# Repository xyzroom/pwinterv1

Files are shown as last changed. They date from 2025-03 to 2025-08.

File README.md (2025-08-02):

# P-Winter V1 (archive)

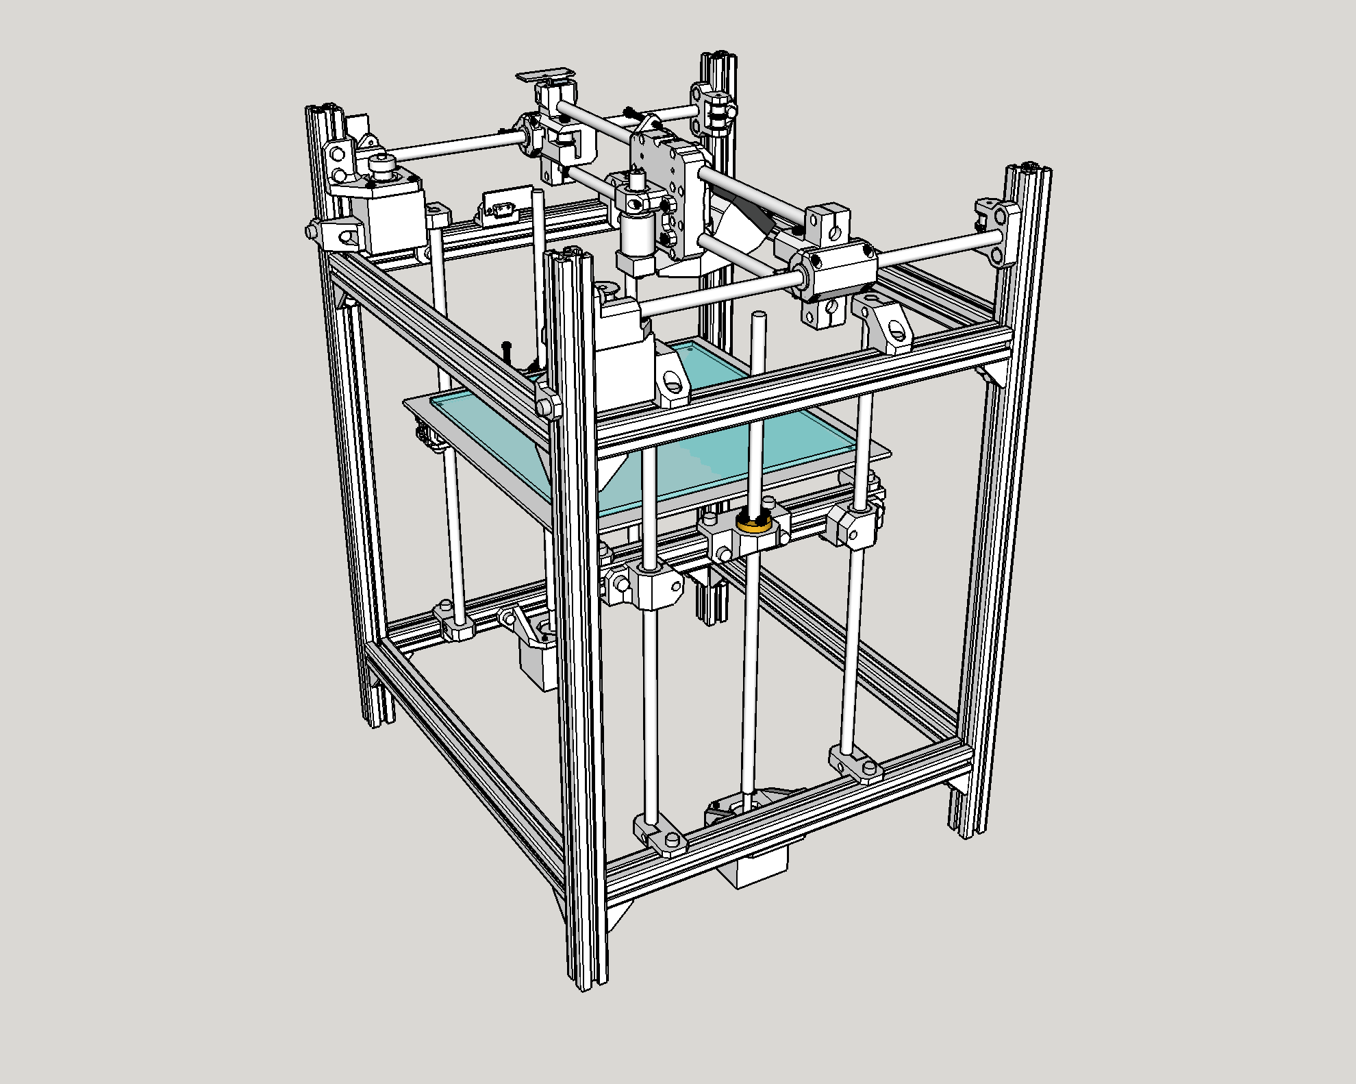
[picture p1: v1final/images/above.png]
front image


## Welcome
- P-Winter is a CoreXY 3D printer. It aims for an accessible BOM and assembly, with drop-in nuts and a fully-bracketed frame.
- There are major flaws with this design. It was made predominantly when I was 14 with zero experience.
- I am working on P-Winter V2, which will reuse most of the components iron out some silly design flaws and misunderstandings from V1. Well, I had basically completed the V2 concept in SketchUp, but when I went to model it properly in Fusion 360, the files had disappeared! >:(
- V1 cost estimate: approx 50 GBP for non-printed parts in the final printer, not including prototyping waste.

# V2 Changes
## Overview
There were a few fatal flaws and inconveniences with V1. V2 strives to fix most of these. V2 primarily aims for a more sensible belt path, a more sensible Z axis, a filtered enclosure, a (larger) more sensible build volume.

## Dimensions and V2 Enclosure
- V1 Frame (2020 T-slot extrusions): 380mm x 340mm x 500mm
- V1 Build volume: approx 210mm x 199mm x 270mm
- V2 will use the same frame with added extrusions for the enclosure and other attachments (e.g. filters).
##
- The V1 frame was not enclosable due to part of the XY spilling out to the sides and to the top.
- V2 changes this, compacting the design while offering a larger build volume. The current build footprint in CAD is at least a comfortable 220mm x 220mm.
- The Z axis is being shortened to enable the toolhead's Bowden tube and wiring to be enclosed comfortably.
- Previously, the electronics for V1 where pulled outside an external enclosure to keep them cool. For V2, the electronics will be hidden at the bottom of the printer, separated from the heated chamber via an air gap.
- Some enclosure circulation/filtration shenanigans.

## CoreXY
- V1 uses 8mm linear rods: 2x 300mm for Y and 2x 350mm for X.
- These are retained for V2. V2 will use LM8LUUs for Y and LM8UUs/LM8LUUs for X.
##
- V1 used 16T GT2 pulleys and idlers and 6mm steel-core GT2 belts, with 38mm NEMA 17 stepper motors.
- The knockoff pulleys and idlers had questionable bearing quality/centred-ness/profile accuracy. Additionally, I had spaced them incorrectly in the previous belt path. The idlers also did not operate smoothly on the threaded bolts I was using to hold them.
- The steel-core belts had questionable thickness and were incompatible with the small bend radius of the 16T pulleys and idlers.
- V2 will use proper belts and use stacked F695 flanged bearings as idlers. These have larger bearings suited for motion, are more likely to be round and centred, and also have more predictable dimensions than cheap toothed idlers. V2 will use dowel pins to hold these idlers properly.
##
- V1 used a Hypercube-based belt path where the AB motors occupied space at the front of the Y axis. The motors were an eyesore and limited the travel in Y.
- The belt path has been completely redrawn for V2. It is now correctly aligned and parallel, and I have brought it as close to the enclosed extremities as possible, increasing travel significantly in both X and Y. The AB motors have been moved to the back of the frame.
- The AB motors no longer need to be aligned with the belt path. The diameter of the pulleys no longer matter either. Either 16T or 20T can be used with minimal modification.
##
- Some magic with the belt path leaves 307mm of available rod length in the X axis. This allows for an 85mm-wide X carriage to travel 220mm comfortably in the X direction.
- The motors being in the back of the frame increases the available rod length to 267mm (up to 282mm). A 45mm-wide Y carriage can confortably travel 220mm in the Y direction.
- These limits can be pushed, but I am sticking to (220mm)^2 for now. The bed is (250mm)^2 so I can modify printer dimensions as desired after I get it working.
##
- In V1, the motor mounts began to deform due to belt tension and motor weight acting together. The V2 motor positioning allows for a stronger, thicker mount with better-placed bolting holes. The belt tension now acts against the weight of the motor.

## Z axis
- V1 used a dual-Z setup with two 8mm x 350mm linear rods and a 350mm leadscrew on each side of the frame. (The 350mm leadscrew is too long for 350mm linear rods when using regular leadscrew nuts but this is not a major issue). This offered approximately 270mm in vertical travel
- V2 will use a similar setup with 4 rods and 2 (maybe 3) leadscrews, but shorten the Z axis to enclose the printer better.
##
- The original V1 -> V2 plan was to implement automatic bed levelling with three independent leadscrews. I decided against this because an effective triple Z requires an additional axis, two additional steppers and two additional drivers. There is a risk of overconstraint and having 3 leadscrews may introduce other artefact problems. Overall these are resources I would prefer to allocate to my 300mm printer project.
- I might still add a ABL sensor to V2.
- A 220mm printer really should just be properly trammed...
##
- The V1 setup used separate Z carriages on each side of the printer, connected only via the heated bed and bed levelling springs. The carriages were atrocious to tram relative to each other and to the frame.
- V2 will use a rectangular frame made from 4 extrusions, with the bed bolted directly to the T-slot channels using silicon spacers. This will be far stiffer and easier to level.

## Toolhead
- V1 used a V6 Volcano clone in a Bowden setup. V2 will keep this or use a HGX-LITE clone in direct drive.
- V1 did not end up with any part cooling. My newbie duct design had nil airflow and collided with the belts in the back, so I got rid of it and left it to V2.
- V2 will use dual 5015s for part cooling.

## Electronics
- The original setup was a classic 12V Mega/RAMPS/A4988 setup running Marlin 2.0. This was undeniably the cheapest possible setup and what I'm used to.
- Marlin took forever to compile. 3-axis hardware is not hard to build, but I'd like to get more involved with the software side of 3D printers. The new setup will run on Klipper and have an ADXL which will be fun.
- I will be switching from 12V to 12V + 24V electronics. The heated bed could barely reach 75 deg C, so I will be supplying 24V to at least the heated bed, and potentially other components if I ever need to push performance.
- Silent stepper drivers.
- Known thermistors rather than mystery 100k.

## V1 Performance and Other V2 Improvements
- Prints suffered from a wobble/layer shifting in the Y direction, on average in the correct position. I suspect this was due to play in the X axis rods and hot end nozzle, misalignment in the belt path and improperly-tuned stepper drivers. In V2, rods and bearings will be clamped down on rather than clipped or press-fitted into place.
- V1 homing used Makerbot-style endstops that are triggered by adjustable bolts on the moving carriage. This precision adjustment was good for the Z axis but unnecessary for the X and Y axes. Switching to simpler triggers.
- In general V2 is a design made by a more experienced me. The parts are more functional and the CAD is more detailed, avoiding issues in V1 where the lack of detail meant that bolts were inaccessible or that things would collide with the belt path. New models check for interference, etc and are much more mature.

## V2 Predicted Issues/Advice To Self
- Centre of mass imbalance on the X rods.
- Check the continuity of endstop switches and the resistance of heaters/thermistors with a multimeter. It took forever to figure out why the linear voltage regulator on my Mega kept frying. There was a solder bridge short circuit on one of my endstops!!!
- Tune steppers properly.

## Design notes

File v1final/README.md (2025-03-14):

# v1 final (dec2024)
## Comments
- 3.2mm holes for M3
- 5mm holes for M5 bolts - In V2, these will be 5.2mm
- 2.9mm holes for screwing M3 into plastic - In V2, this will be replaced by circles with tabs
- Dowel pins for idlers in V2
- In V2, built-in bridge supports for overhanging holes will be replaced.
- In V2, eliminated circular overhangs
- In V2, consider notches in tight fit holes to prevent seam line interferance

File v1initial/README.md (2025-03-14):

# v2 initial
## Comments
These are initial files for the machine, barely usuable.
- The old x carriage had issues gripping onto the linear bearings and flexed under belt tension. The new x carriage clamps on the bearings and is not missing so much material.
- The new hot end mount grips onto the E3D V6 cooling fins using a zip tie for added stability.
- The new y carriages clamp onto the x linear rods, adding stability.
- The y rod/roller mounts are now more reliable to align with the frame.
- Some distances have been changed, with some yet to change

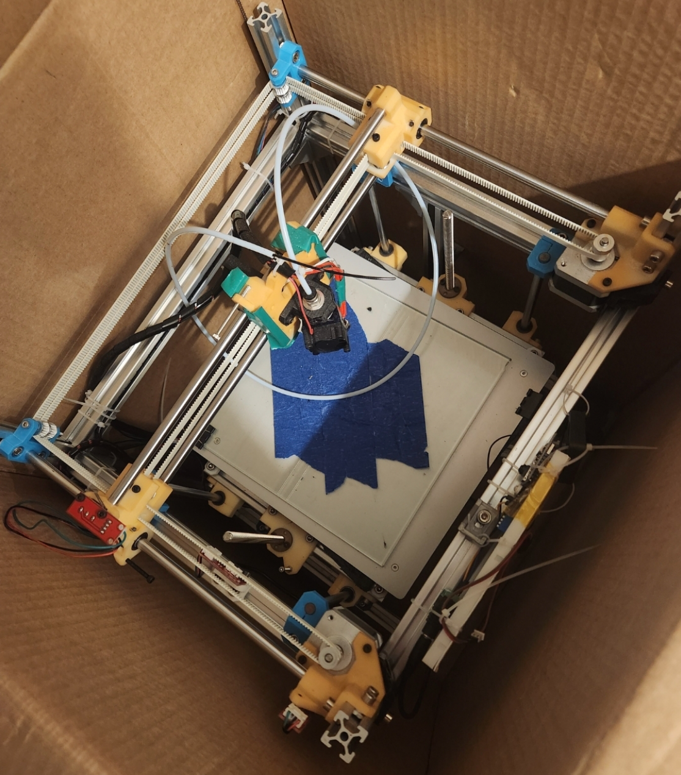
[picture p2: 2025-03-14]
v1final/images/wide.png

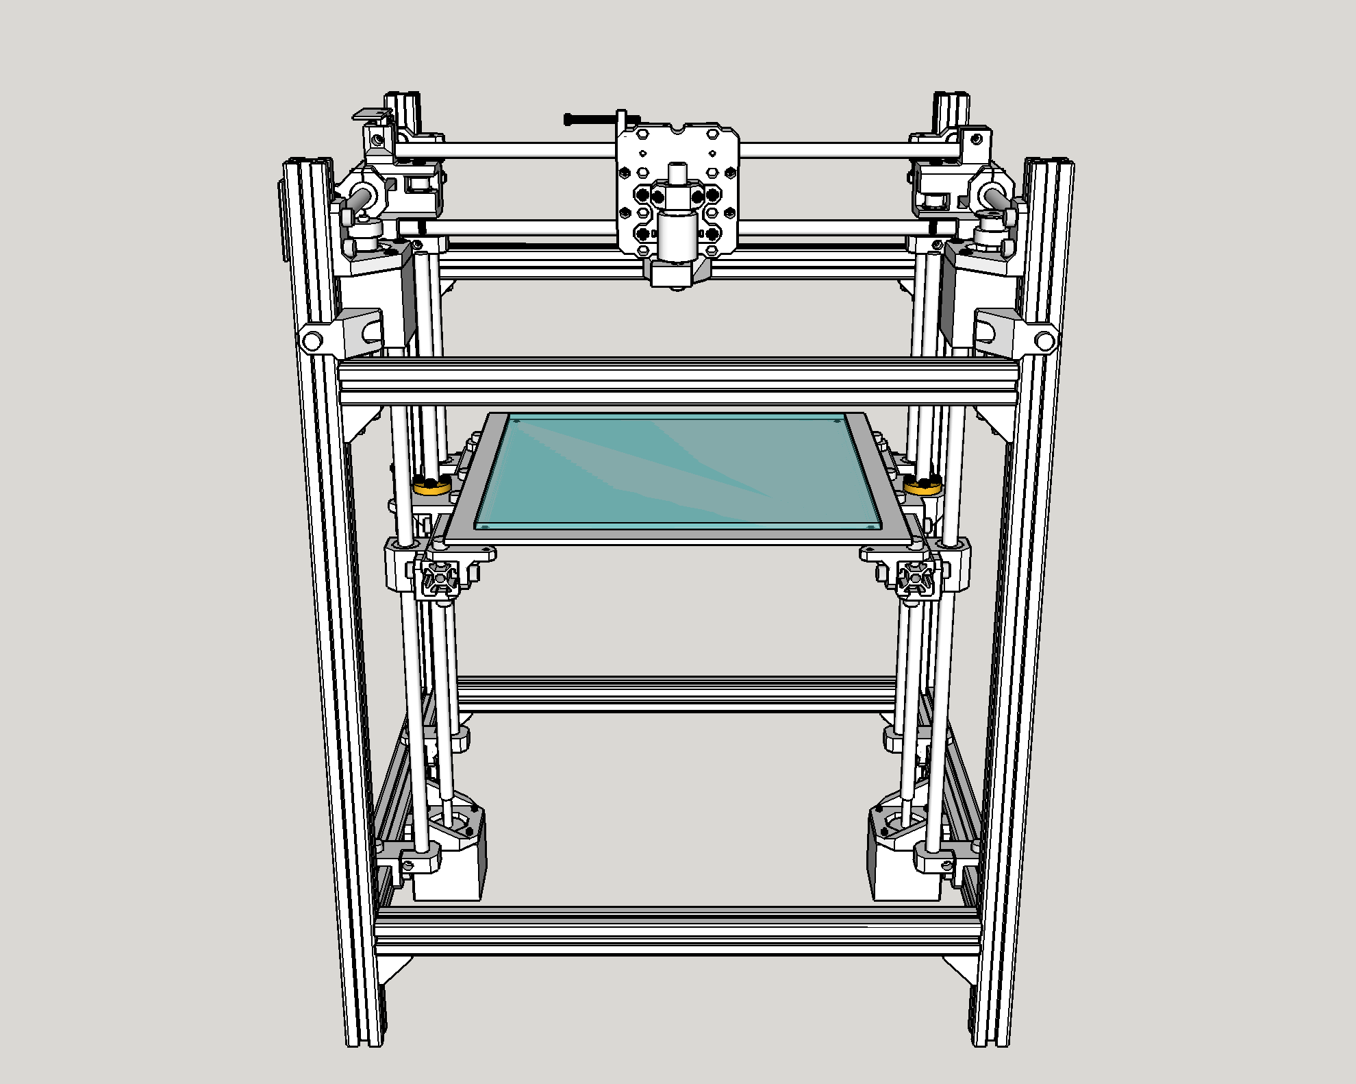
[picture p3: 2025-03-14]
v1final/images/front.png

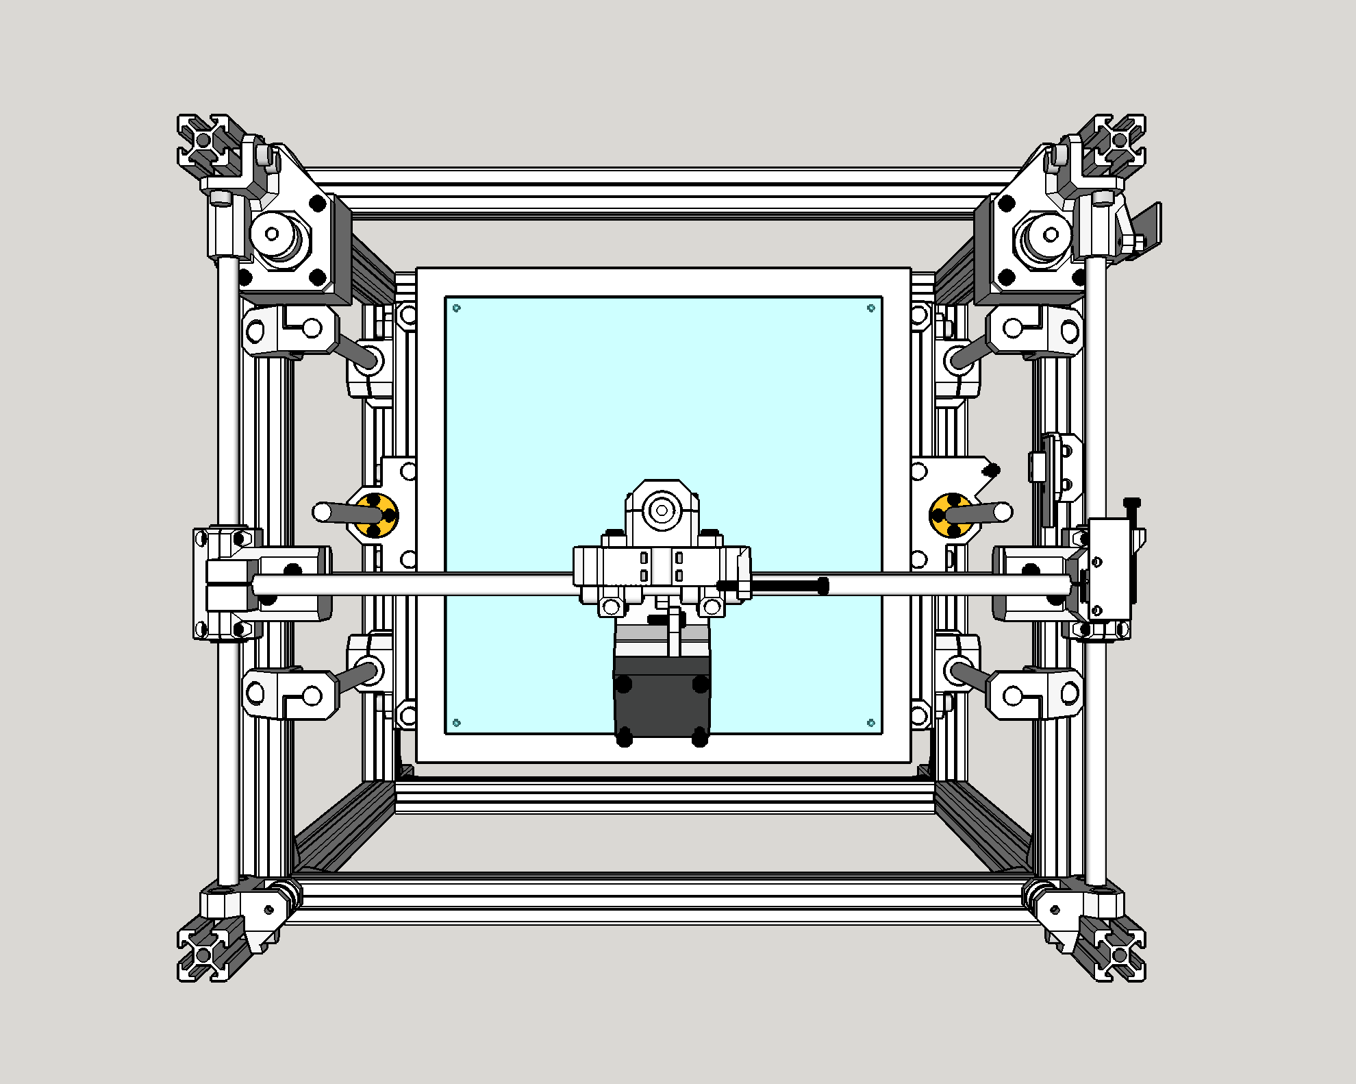
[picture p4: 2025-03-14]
v1final/images/top.png

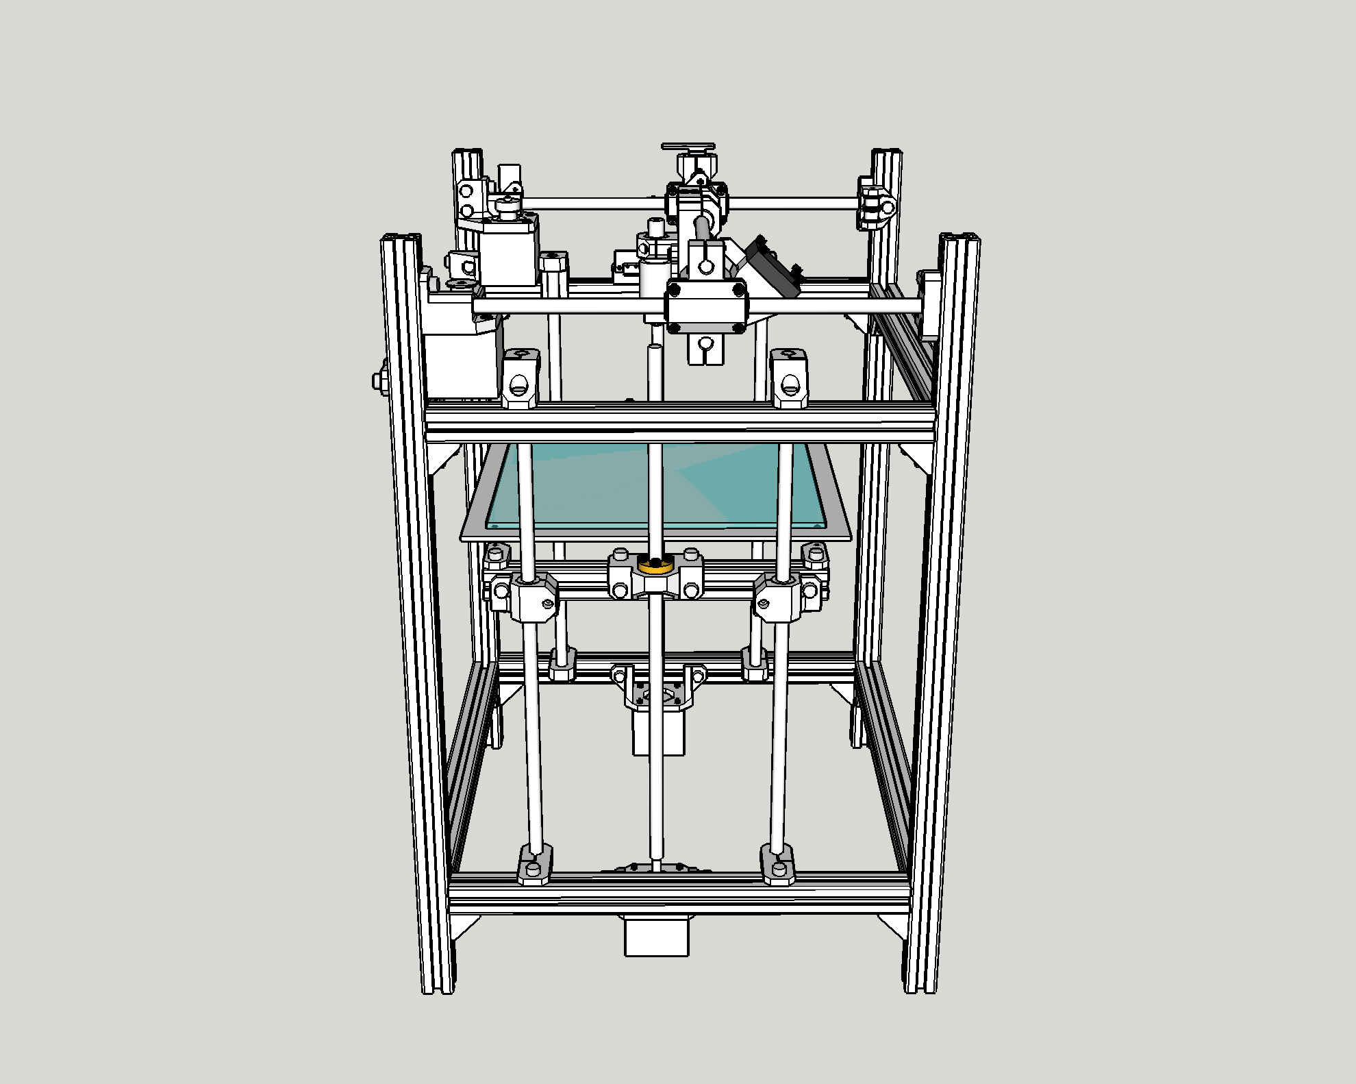
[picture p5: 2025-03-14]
v1final/images/side.png

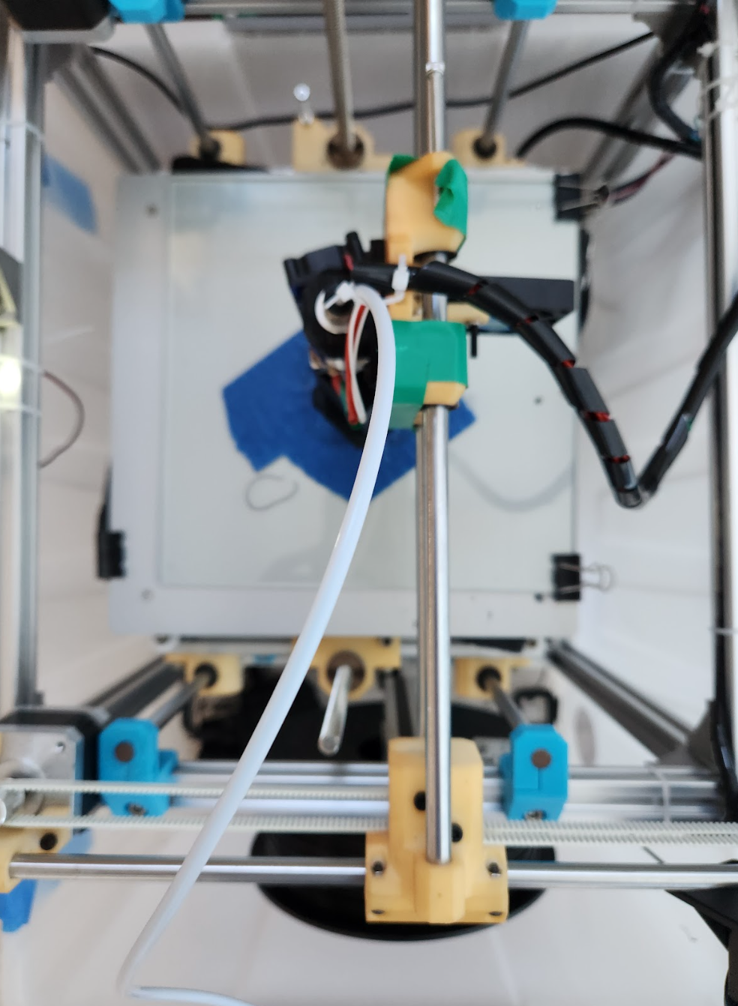
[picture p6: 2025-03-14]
v1final/images/toppicture.png

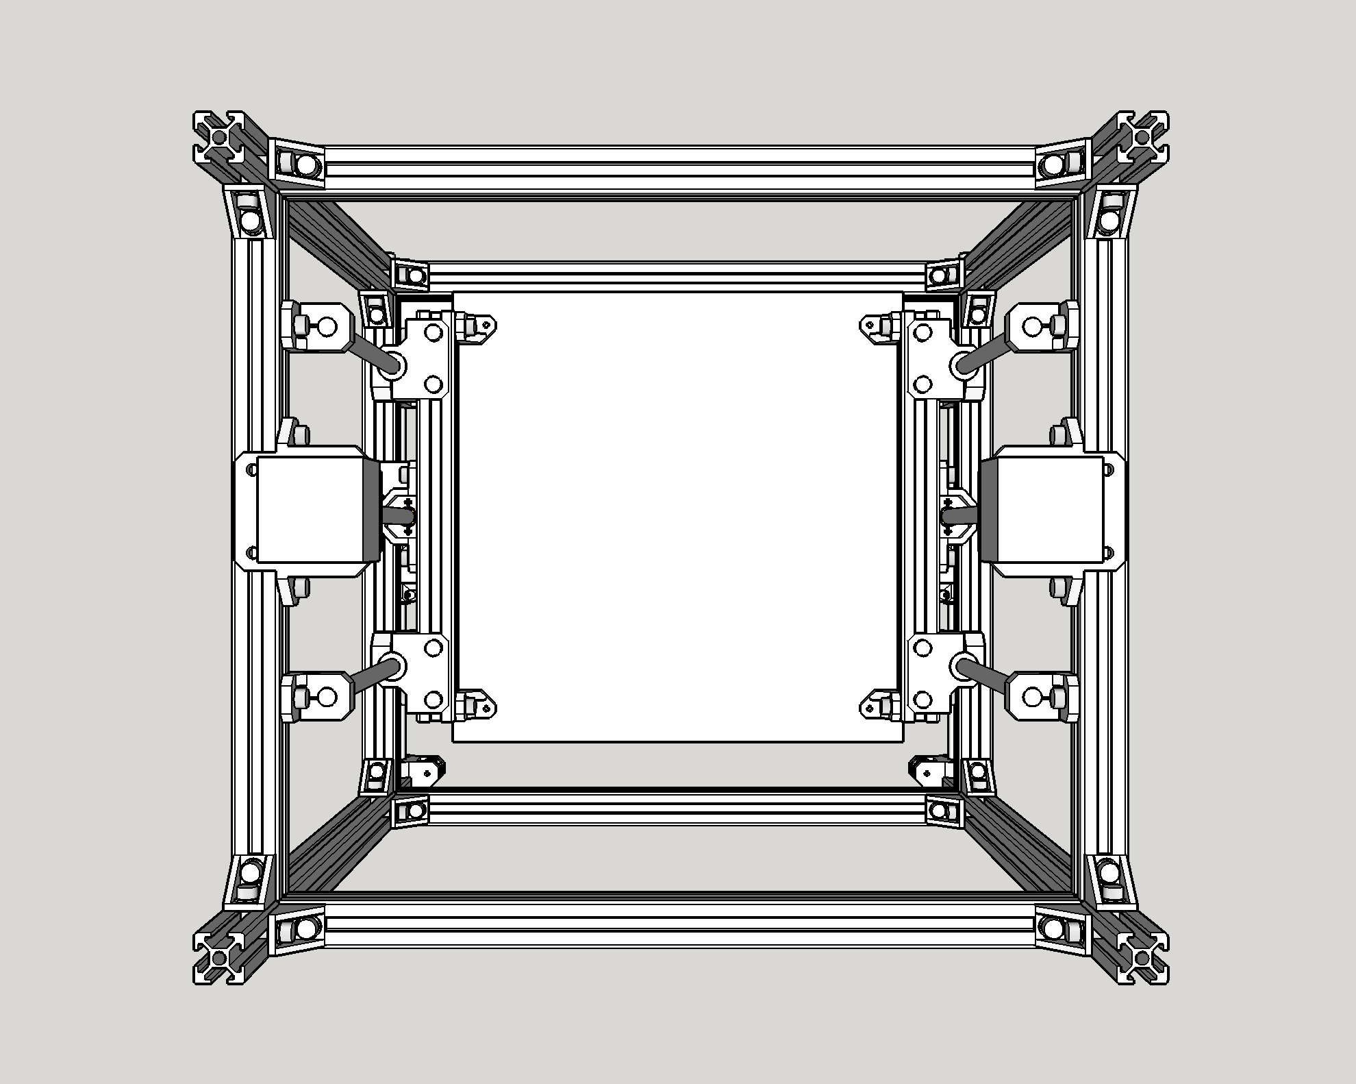
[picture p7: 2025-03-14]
v1final/images/bottom.png

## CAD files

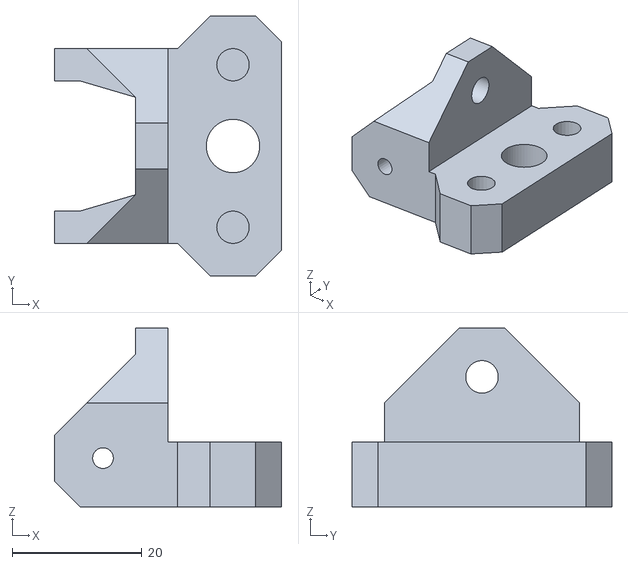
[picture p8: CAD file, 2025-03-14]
v1final/STLs/y roller mount x2.stl
35.0 x 40.0 x 27.5

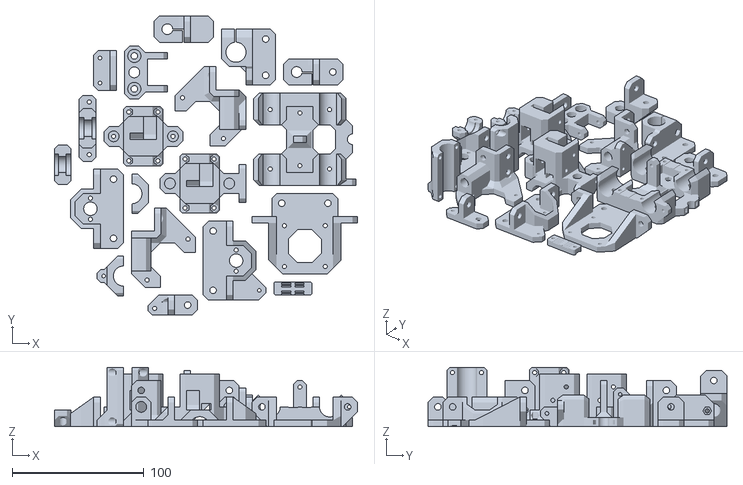
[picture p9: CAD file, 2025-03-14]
v1initial/platedbadlyold.stl
229.8 x 226.7 x 45.0

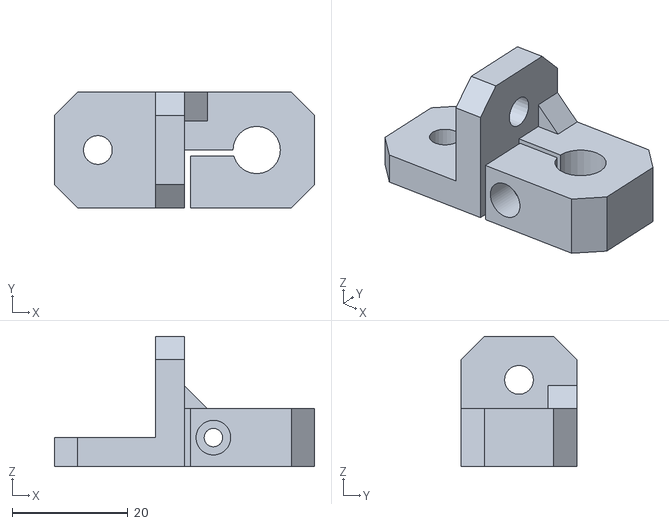
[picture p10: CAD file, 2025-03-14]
v1final/STLs/z rod mount bottom x2 and x2 mirrored.stl
45.0 x 20.0 x 22.5

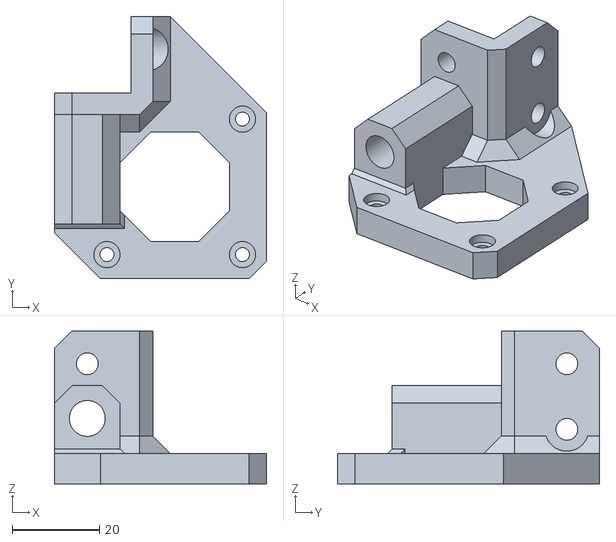
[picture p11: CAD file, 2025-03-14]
v1final/STLs/y motor mount right.stl
48.5 x 60.0 x 35.0

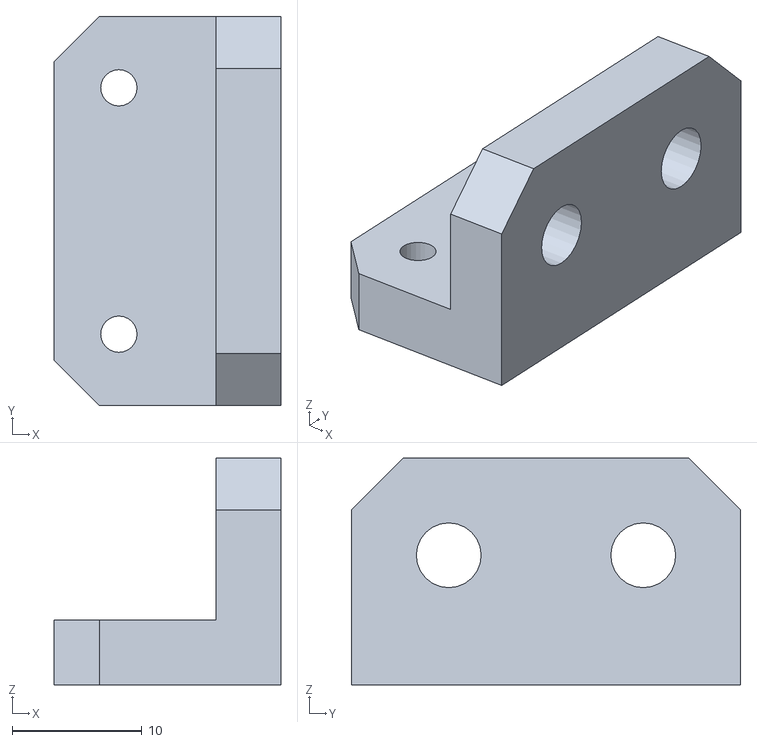
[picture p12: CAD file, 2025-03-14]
v1final/STLs/z endstop mount.stl
17.5 x 30.0 x 17.5

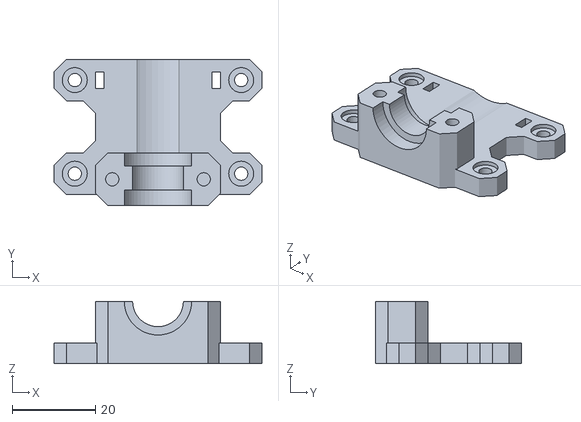
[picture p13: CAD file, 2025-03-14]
v1final/STLs/e3d mount.stl
50.0 x 35.2 x 15.0

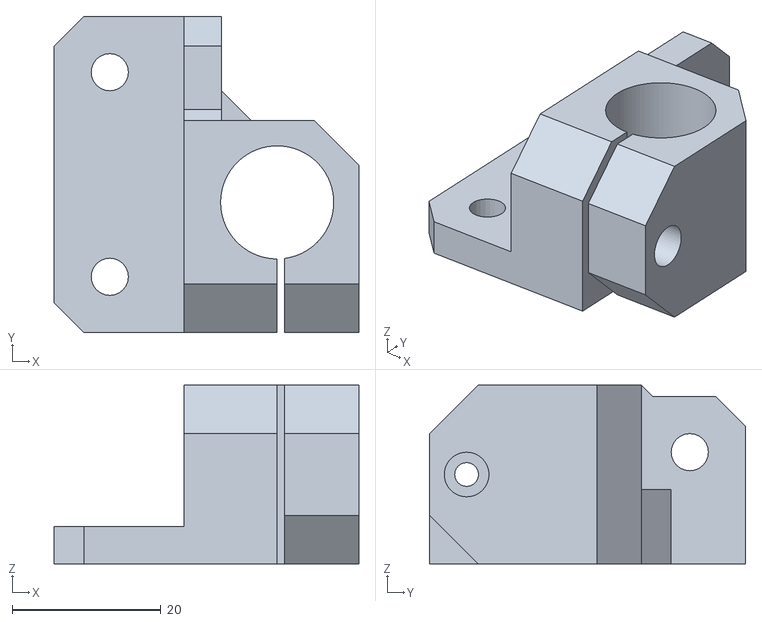
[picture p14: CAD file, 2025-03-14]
v1final/STLs/z bearing mount x2 and x2 mirrored.stl
41.0 x 42.5 x 24.0

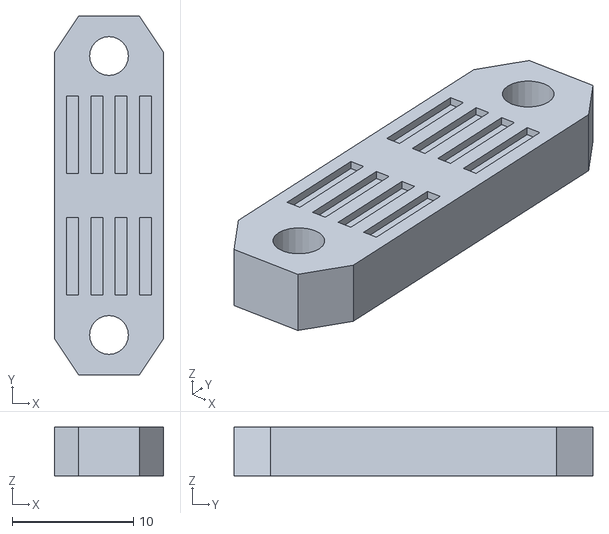
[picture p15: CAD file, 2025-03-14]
v1final/STLs/x belt clamp x2.stl
9.00 x 29.6 x 4.00

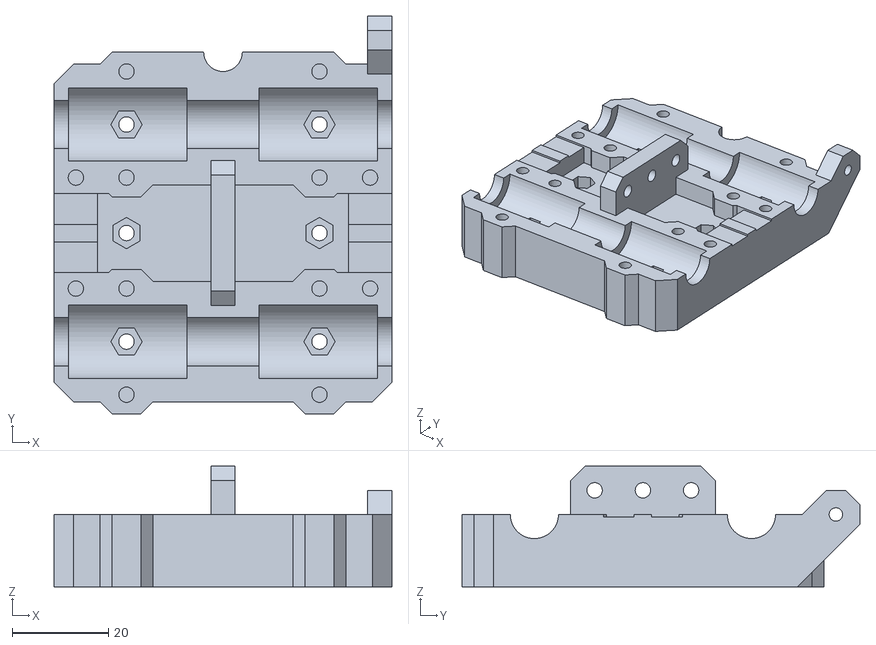
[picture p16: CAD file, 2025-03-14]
v1final/STLs/x carriage.stl
70.0 x 82.5 x 25.0

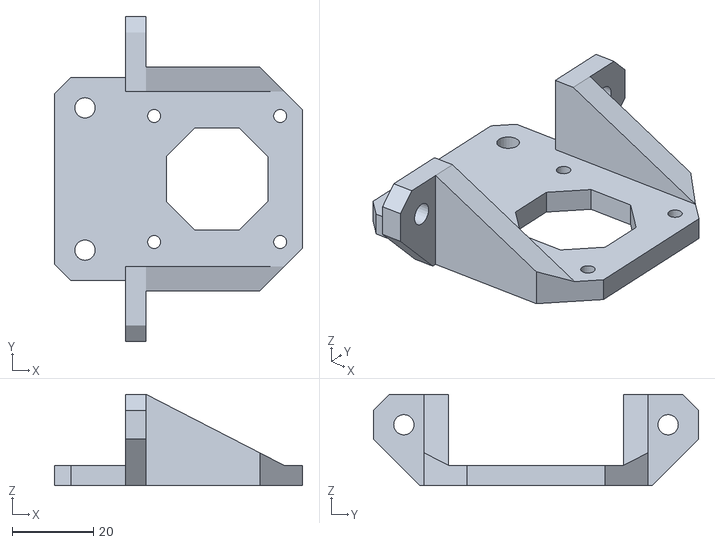
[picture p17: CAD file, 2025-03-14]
v1final/STLs/z motor mount x2.stl
61.0 x 80.0 x 22.5

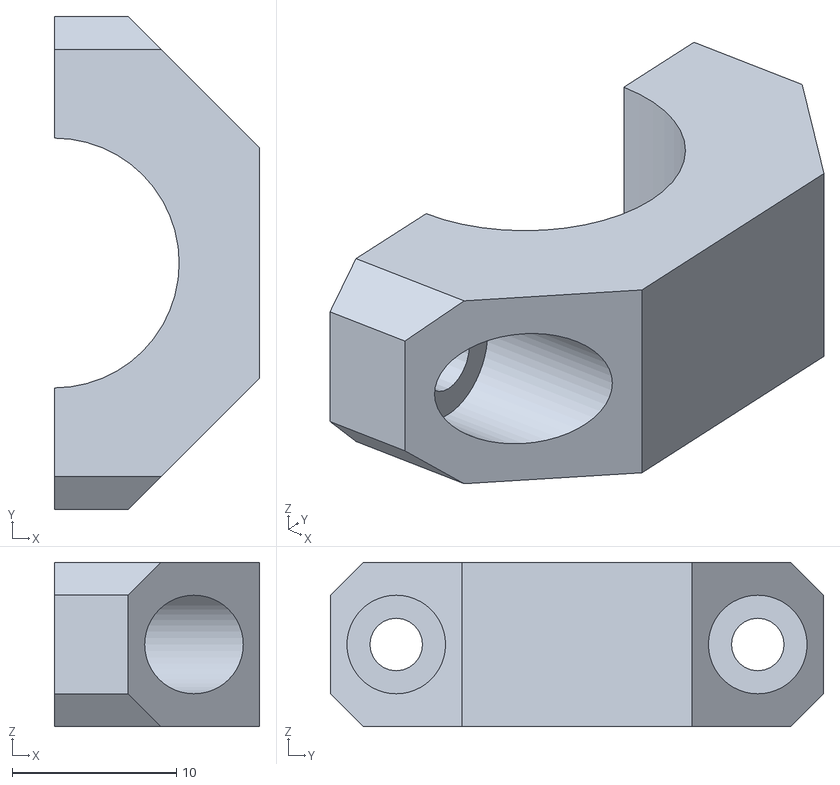
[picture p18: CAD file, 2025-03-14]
v1final/STLs/x bearing clamp x4.stl
12.5 x 30.0 x 10.0

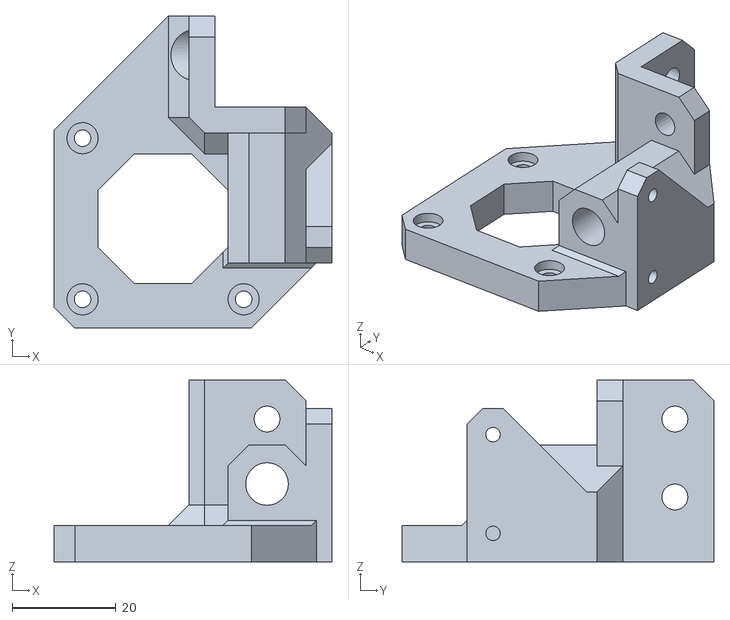
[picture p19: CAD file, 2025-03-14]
v1final/STLs/y motor mount left.stl
53.5 x 60.0 x 35.0

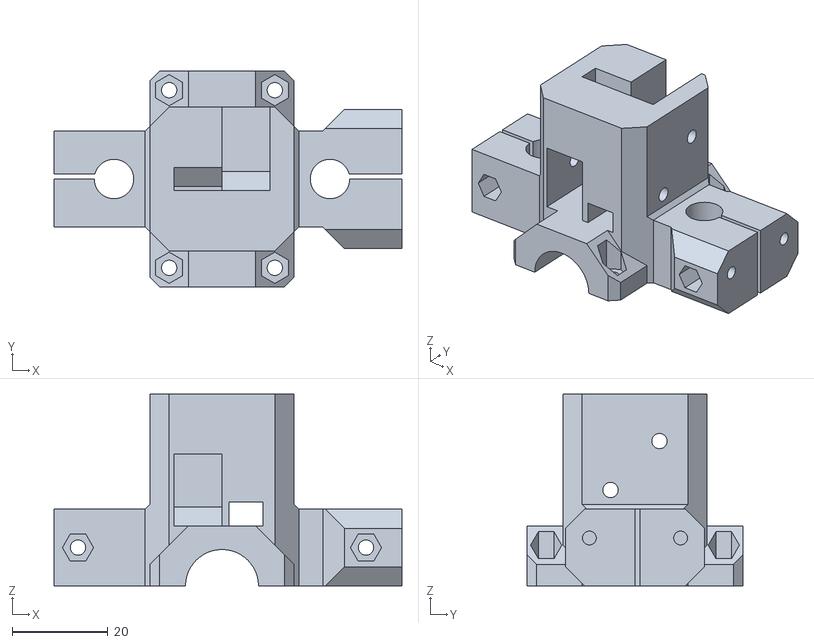
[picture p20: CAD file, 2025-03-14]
v1final/STLs/y carriage left.stl
72.5 x 45.0 x 40.0

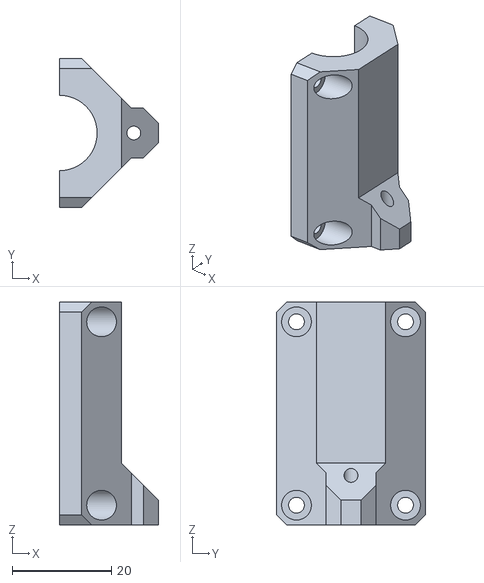
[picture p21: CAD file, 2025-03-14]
v1final/STLs/y bearing clamp left.stl
20.0 x 30.0 x 45.0

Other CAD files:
v1final/STLs/y bearing clamp right.stl
v1final/STLs/bed mount x2 and x2 mirrored.stl
v1final/STLs/z rod mount top x2 and x2 mirrored.stl
v1final/STLs/y carriage right.stl
v1final/STLs/e3d clamp.stl
v1final/STLs/z nut mount left.stl
v1final/STLs/z nut mount right.stl
